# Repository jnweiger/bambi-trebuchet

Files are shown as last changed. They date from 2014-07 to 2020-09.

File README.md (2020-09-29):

bambi-trebuchet
===============

My first fully operational trebuchet design. Inexpensive, lightweighted, all made from wood. Very efficient with tennis balls, waterbombs, or (boiled) eggs..

https://en.opensuse.org/images/2/20/Trebuchet_simulation_slides.pdf

https://www.thingiverse.com/thing:3761789

https://www.youtube.com/watch?v=IiG2VPLTDpg

https://www.youtube.com/watch?v=-Pv-yPBlofo

https://www.youtube.com/watch?v=MHek-5BepOQ

https://www.youtube.com/watch?v=J0sa-UWGPxY

https://www.youtube.com/watch?v=l8cluoF6mdc

https://www.youtube.com/watch?v=qAsLDPJmh3s

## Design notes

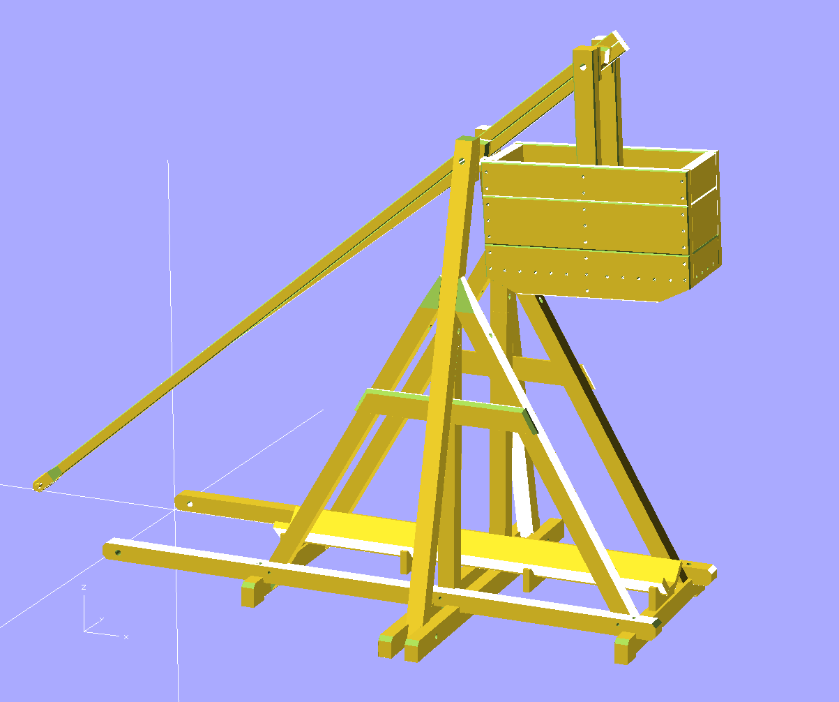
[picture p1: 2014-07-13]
frame.png

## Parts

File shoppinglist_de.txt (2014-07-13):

Holz:

* 44x44 mm Fichtenleiste (ca 15m?) http://www.hornbach.de/shop/Kantholz-Fichte-gehobelt-44x44x2500-mm/1001281/artikel.html
* 28x28 mm Fichtenleiste (ca 4m) http://www.hornbach.de/shop/Quadratstab-Fichte-roh-28x28x2000-mm/5485726/artikel.html
* 53x34 mm Fichtenleiste (bottom bars, + box)
* 60x18 mm Fichtenbrett (ca 5m) http://www.hornbach.de/shop/Glattkantbrett-Fichte-gehobelt-60x18x2500-mm/5154622/artikel.html
* 14 mm Rundstab geriffelt. (ca 2m?) 
* 16 mm Rundstab Buche glatt. (ca 1m) www.hornbach.de/shop/Rundstab-Buche-roh-16-mm-L1000-mm/5485762/artikel.html
* 10 mm Dübel (20pc?) http://www.hornbach.de/shop/Langholzbuebel-Wolfcraft-8-mm-150er-Pack/980507/artikel.html
* 174x27 mm Fichtenbrett (ca 10m) http://www.hornbach.de/shop/Universalbrett-Fichte-174x27x2000-mm/5154629/artikel.html

Metall:

* Ring ca 10-20mm
* Rundstift 2mm, 30mm lang
* Ringschraube 3mm, 12mm, 20mm (4 Stück)
* 15x3 mm Flacheisen 80mm lang, (Auslösehaken)

Misc:

* 200 x 400 mm Jeansstoff
* 2mm Schnur, ca 10m
* 4mm Schnur, ca 1m

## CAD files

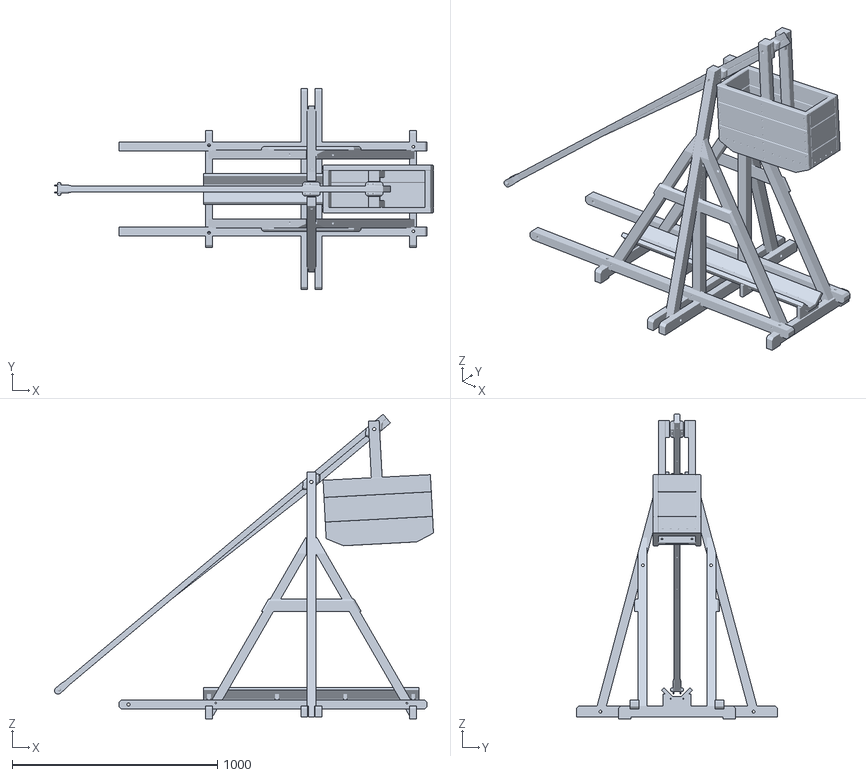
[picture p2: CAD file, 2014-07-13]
frame.stl
1847.0 x 980.0 x 1485.0

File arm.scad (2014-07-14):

// (c) 2014 juewei@fabfolk.com
//
// catapult arm for bambi trebuchet
//
// FIXME: arm_pyramid should be made of multiple layers
//        "sperrverleimt."

use <bbox.scad>

$fs=1;	// segment size: 1mm

d1=8;	// bolt diameter for gluing walls
endl=70;
dh=14;		// diameter of pin holder

// origin is center of main shaft.
// l1=1624/l2=325 ratio is 1:5
module arm_double_beam(l1=1625, l2=325, d=28)
{
  l=l1+l2+endl;
  lx=980;

  translate([-endl-l2, -d/2, 0]) union()
    {
      difference()
	{
	  union()
	    {
              bbox(l,d,d,bx=2);
	      translate([0,0,-28]) bbox(lx,d,d,bx=2);
	    }
	  translate([lx,-10,0]) rotate([0,180-4,0]) cube([lx,d+20,d+20]);
	  translate([endl+l2,-50,0]) rotate([-90,0,0]) cylinder(d+100,8,8);
	  translate([endl,-50,0])    rotate([-90,0,0]) cylinder(d+100,8,8);
	  for (x = [endl/2 : 210 : lx-endl])
	    {
	      translate([x,d/2,-28-10]) cylinder(d+10+10, 3,3);
	    }
	}
    }
}

module arm_head_side(w=28,s=8)
{
  difference()
    {
      union()
        {
          translate([-3*w,0,0]) cube([3*w,s,w]);
          translate([-3*w,s/2,w]) rotate([0,90,0]) cylinder(3*w,s/2,s/2);
          translate([-3*w,s/2,0]) rotate([0,90,0]) cylinder(3*w,s/2,s/2);
          translate([   0,s,w/2]) rotate([90,0,0])  cylinder(s,w/2,w/2);
	  translate([ 0,s/2,w/2]) rotate([90,0,0]) rotate_extrude() translate([w/2, 0, 0]) circle(r = s/2);
        }

      // hole for pin holder
      translate([-dh/2,10,w/2]) rotate([90,0,0]) cylinder(s+10,dh/2,dh/2);

      // flatten left right outside
      translate([-3*w,0,-10]) rotate([0,0,10]) cube([3*w,s+10,w+s+20]);
      
      // taper top 
      translate([-3*w,-5,w-3]) rotate([0,-7,0]) cube([3*w,s+10,w+s+20]);

      // taper bottom
      translate([-3*w,-5,3])  rotate([0,90+7,0]) cube([w+s+20,s+10,3*w]);
    }
}

module arm_pin_holder(w=28,s=6,d=6)
{
  l=w+2*d+2*s+1*s;
  k=1;
  dp=2;
  difference()
    {
      union()
        {
          translate([0,-l/2,0]) rotate([-90,0,0]) cylinder(l,dh/2,dh/2);
	  // add conical end caps.
          translate([0, l/2,0]) rotate([-90,0,0]) cylinder(3,dh/2,dh/2-3);
          translate([0,-l/2,0]) rotate([ 90,0,0]) cylinder(3,dh/2,dh/2-3);
	}
      // holes accros for the taps
      translate([0,-w/2-s-d/2+k,-dh/2-10]) cylinder(dh+20,d/2,d/2);
      translate([0,w/2+s+d/2-k,-dh/2-10]) cylinder(dh+20,d/2,d/2);

      // hole for the pin itself
      rotate([0,90,0]) translate([0,0,-dh/2-10]) cylinder(dh+20,dp/2,dp/2);
    }
}

module arm_head(w=28, alpha=6)
{
  translate([0, (w)/2,0])                 arm_head_side(w,6);
  translate([0,-(w)/2,0]) scale([1,-1,1]) arm_head_side(w,6);
  translate([-dh/2,0,w/2]) rotate([0,-alpha,0]) arm_pin_holder();
}

module arm_pyramid(h=20)
{
  dm=16; 	// diameter of main shaft
  difference()
    {
      intersection()
        {
          rotate([0,45,0]) translate([-40,-10,-40]) bbox(80,h+10,80,bx=8,bz=8);
          // cut away top and bottom 
          translate([-60,-28+10,-28]) cube([120,2*28,2*28]);
          rotate([45,0,0]) translate([-60,-28,-28]) cube([120,2*28,2*28]);
	}
      // cut away the inside bevel of bbox.
      rotate([0,45,0]) translate([-50,-20,-50]) cube([100,20,100]);

      // main shaft hole in pyramid
      rotate([-90,0,0]) translate([0,0,-10]) cylinder(h+20,dm/2,dm/2);

      // holes for cross setion bolts, glued
      translate([dm,h/2,-28-10]) cylinder(2*28+20,d1/2,d1/2);
      translate([-dm,h/2,-28-10]) cylinder(2*28+20,d1/2,d1/2);
    }
}

// origin is center of main shaft.	
// l1=1624/l2=325 ratio is 1:5
module arm(l1=1625, l2=325)
{
  arm_double_beam(l1-20, l2, d=28);
  translate([l1,0,0]) arm_head(w=28,alpha=12);
  translate([0, 28/2, 0])                 arm_pyramid();
  translate([0,-28/2, 0]) scale([1,-1,1]) arm_pyramid();
  translate([-l2, 28/2, 0])                 arm_pyramid();
  translate([-l2,-28/2, 0]) scale([1,-1,1]) arm_pyramid();
}

arm();

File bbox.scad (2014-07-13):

// (c) 2014 juewei@fabfolk.com
//
// a bevelled (or camfered) box

module bbox_chamfer_cutaway_z(x,y,z,b)
{
  translate([b,0,-10]) rotate([0,0,90+45]) cube([2*b,2*b,z+20]);
  translate([x-b,0,-10]) rotate([0,0,-45]) cube([2*b,2*b,z+20]);

  translate([b,y,-10]) rotate([0,0,90+45]) cube([2*b,2*b,z+20]);
  translate([x-b,y,-10]) rotate([0,0,-45]) cube([2*b,2*b,z+20]);
}

module bbox_x(x,y,z,b)
{
  difference()
    {
      cube([x,y,z]);
      translate([0,0,z])rotate([0,90,0]) bbox_chamfer_cutaway_z(z,y,x,b);
    }
}

module bbox_y(x,y,z,b)
{
  difference()
    {
      cube([x,y,z]);
      translate([0,y,0])rotate([90,0,0]) bbox_chamfer_cutaway_z(x,z,y,b);
    }
}

module bbox_z(x,y,z,b)
{
  difference()
    {
      cube([x,y,z]);
      bbox_chamfer_cutaway_z(x,y,z,b);
    }
}

module bbox(x,y,z,b=0,bx=0,by=0,bz=0)
{
  difference()
    {
      cube([x,y,z]);
      if (b > 0)
        {
          translate([0,0,z])rotate([0,90,0]) bbox_chamfer_cutaway_z(z,y,x,b);
          translate([0,y,0])rotate([90,0,0]) bbox_chamfer_cutaway_z(x,z,y,b);
          bbox_chamfer_cutaway_z(x,y,z,b);
	}

      if (bx > 0) translate([0,0,z])rotate([0,90,0]) bbox_chamfer_cutaway_z(z,y,x,bx);
      if (by > 0) translate([0,y,0])rotate([90,0,0]) bbox_chamfer_cutaway_z(x,z,y,by);
      if (bz > 0) bbox_chamfer_cutaway_z(x,y,z,bz);
    }
}

bbox(100,200,250, bx=5,by=10,bz=1);

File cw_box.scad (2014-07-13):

// (c) 2014 juewei@fabfolk.com
//
// counterweight box for bambi trebuchet

use <bbox.scad>

d1=8;	// bolt diameter for gluing walls

module cw_box_handle(wn=1.5,hn=3,l=400,bw=174,bz=27,h=450)
{
  w = bw*wn;

  difference()
    {
      union()
	{
	  translate([-53/2,-w/2,0])          bbox(53,34,h,bz=3);
	  translate([-53/2, w/2-34,0])       bbox(53,34,h,bz=3);
	  translate([-53/2,-w/2+34,h-80])    bbox(53,20,80,bz=3);
	  translate([-53/2, w/2-34-20,h-80]) bbox(53,20,80,bz=3);

	  translate([ 53/2,-w/2,0])    bbox(44,w,44,by=3);
	  translate([-44-53/2,-w/2,0]) bbox(44,w,44,by=3);
	}
      
      // hole for rear shaft
      translate([0,0,h-80/2]) rotate([90,0,0]) translate([0,0,-w/2-10]) cylinder(w+20,8,8);

      // base bolt holes, glued
      translate([0, w/2-34/2,44/2]) rotate([0,90,0]) translate([0,0,-100]) cylinder(200,5,5);
      translate([0,-w/2+34/2,44/2]) rotate([0,90,0]) translate([0,0,-100]) cylinder(200,5,5);
    }
}

module cw_box_floor(wn,l,bw,bz)
{
  w=wn*bw;
  w2 = floor(wn)*bw;

  translate([-l/2, -w/2, 0]) difference()
    {
      union()
	{
	  for (y = [0 : bw : w-bw])
	    {
	      translate([0,y,0]) bbox(l,bw,bz,bx=3);
	    }
	  if (w2 < w)
	    {
	      translate([0,w2,0]) bbox(l,w-w2,bz,bx=3);
	    }
	}
      translate([l/2-(53+1)/2, -10,-10]) cube([53+1,34+1+10,bz+20]);
      translate([l/2-(53+1)/2, w-34-1,-10]) cube([53+1,34+1+10,bz+20]);
    }
}

module cw_box_long_wall(l, bw, hn, bz)
{
  alpha=25;
  h = hn*bw;
  h2 = floor(hn)*bw;

  difference()
    {
      union()
        {
	  for (y = [0 : bw : h-bw])
	    {
	      translate([0,0,y]) bbox(l+2*bz,bz,bw,bx=3,bz=3);
	    }
	  if (h2 < h)
	    {
	      translate([0,0,h2]) bbox(l+2*bz,bz,h-h2,bx=3,bz=3);
	    }
        }
      translate([0,0,44-5])      rotate([0,alpha,0])  translate([0,-10,-10-44]) cube([120,bz+20,10+44]);
      translate([l+2*bz,0,44-5]) rotate([0,90-alpha,0]) translate([0,-10,-120]) cube([44+10,bz+20,120]);
      for (y = [20 : 40 : h])
        {
          for (x = [bz/2 : (l+bz)/2 : l+2*bz])
	    {
	      translate([x,-10,y]) rotate([-90,0,0]) cylinder(bz+20, d1/2, d1/2);
	    }
	}
      for (x = [50 : 40 : l/2])
        {
	   translate([x,-10,44+bz/2]) rotate([-90,0,0]) cylinder(bz+20, d1/2, d1/2);
	   translate([l+2*bz-x,-10,44+bz/2]) rotate([-90,0,0]) cylinder(bz+20, d1/2, d1/2);
	}
    }
}

module cw_box_short_wall(w, bw, hn, bz)
{
  alpha=25;
  h = hn*bw;
  h2 = floor(hn)*bw;

  difference()
    {
      union()
        {
	  for (y = [0 : bw : h-bw])
	    {
	      translate([0,0,y]) bbox(bz,w,bw,by=3);
	    }
	  if (h2 < h)
	    {
	      translate([0,0,h2]) bbox(bz,w,h-h2,by=3);
	    }
	}
      translate([0,0,44-5]) rotate([0,alpha,0]) translate([0,-10,-10-44]) cube([44+10,w+20,10+44]);
      for (y = [20 : 40 : w])
        {
	   translate([-10,y,44+bz/2]) rotate([0,90,0]) cylinder(bz+20, d1/2, d1/2);
	}
    }
}

module cw_box(wn=2,hn=2.7,l=470,bw=120,bz=27,h=520)
{
  w=wn*bw;
  translate([0,0,44]) cw_box_floor(wn,l,bw,bz);
  cw_box_handle(wn,hn,l,bw,bz,h);
  translate([-l/2-bz,w/2    ,0]) cw_box_long_wall(l, bw, hn, bz);
  translate([-l/2-bz,-w/2-bz,0]) cw_box_long_wall(l, bw, hn, bz);
  translate([-l/2-bz,-w/2   ,0]) cw_box_short_wall(w, bw, hn, bz);
  translate([ l/2+bz,-w/2   ,0]) scale([-1,1,1]) cw_box_short_wall(w, bw, hn, bz);
}

cw_box();

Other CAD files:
frame.scad
slide.scad

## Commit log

2014-06-30 First draft of bill of materials. German only. Sorry.
2014-06-30 scetched not to scxale
    [frame.scad]
2014-07-01 finished Längsholm
    [frame.scad]
2014-07-01 Added side supports 15 deg leaning inwards
    [frame.scad]
2014-07-01 all for bottom bars added
    [frame.scad]
2014-07-01 github, can you render stl for me?
    [frame.stl]
2014-07-12 Seitliche dreiecke vorskizziert. Parametriesierung verbessert.
    [frame.scad]
2014-07-12 center_post done.
    [frame.scad]
2014-07-12 cross_board added to the triangles.
    [frame.scad]
2014-07-12 * upper wedge adjusted 3mm, * side_x reduced from 220 to 176, ouch....
    [frame.scad]
2014-07-12 triangle_post completed. fine tuning. side_beta (of triangle_post) is now exaxtly 30° No more pointy ends of triangle_post. The material is always a bit short, so that the ends are blunt.
    [frame.scad, frame.stl]
2014-07-13 bevelled top edge of cross_board
    [frame.scad]
2014-07-13 slide added. Coming from imported file.
    [slide.scad]
2014-07-13 refreshed stl
    [frame.scad, frame.stl, slide.scad]
2014-07-13 added a universal bbox: a cube with adjustable bevel
    [bbox.scad]
2014-07-13 counterweight box added. Using bbox.
    [bbox.scad, cw_box.scad, frame.scad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]
2014-07-13 arm done
    [arm.scad]
2014-07-13 mounted arm_with_box with movable hinges yeah!
    [cw_box.scad, frame.scad]
2014-07-13 exports updated.
    [frame.stl]
2014-07-14 Adjusted arm dimensions to match one of the originals: Ratio 1:5 (short:long)
    [arm.scad]
2014-07-14 exaxt 1:5 ratio
    [arm.scad]
2019-07-21 Added a 39cm version of the Catapult. For easier remakes with your local lasercutter.
